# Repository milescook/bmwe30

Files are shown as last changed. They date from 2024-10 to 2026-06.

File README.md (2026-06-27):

# About

This repo is a collection of diagrams, wiring plans and 3d printable models. The objective is converting a BMW E30 to use speeduino with a digital dashboard using ts-dash. This uses the original Motronic 1.3 harness to de-risk the conversion. 

Disclaimer: Anything you follow here you do at your own risk etc.

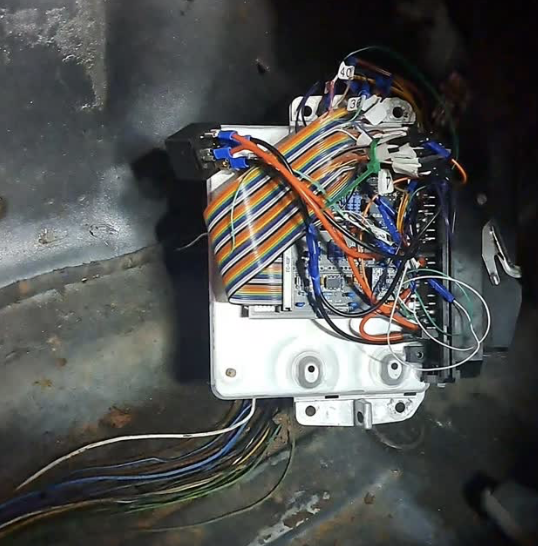
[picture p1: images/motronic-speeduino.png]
Motronic Speeduino


## Wiring
The only wiring modification needed so far, is a replacement injector sub-loom (later harnesses use a sub loom with a connector - see injector wiring for depin tool), and the TPS wires either needs an adapter or re-wire to work with an E36 variable TPS. I also converted the AFM plug to a generic connector though you could always make an adapter.

You can find a load of shorts and videos on progress here [https://www.youtube.com/cookracinguk](https://www.youtube.com/cookracinguk)

## Contents

These are the key items though take a look through the file list for bits and bobs. There's an initial stab at a custom harness for example.

- [Motronic pins to Speeduino map](docs/motronic-speeduino-map.md)
- [Cluster Conversion](docs/cluster.md)
- [Ignition module](docs/ignition.md)
- [Intake](docs/intake.md)
- [Injector wiring](docs/injector-wiring.md)
- [Main relay](docs/mainrelay.md)
- [Useful links](docs/links.md)

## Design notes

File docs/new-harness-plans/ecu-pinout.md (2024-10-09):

# ECU Pinout
* 34 pins on 4 rows, 9, 8, 9, 8. Pin number and wire colour (if present)

 [_1YE]  [_2BL]  [_3GR]  [_4WH]  [_5RD]  [_6BK]  [_7YE]  [_8BL]  [_9--]

*  [10--]  [11--]  [12BK]  [13RD]  [14--]  [15--]  [16YE]  [17BL]  
   
   [18--]  [19BL]  [20WH]  [21BL]  [22BK]  [23SG]  [24--]  [25SS]  

 [26RD] [27BK] [28--]  [29--]  [30GR]  [31RD]  [32WH]  [33GR]  [34WH]
  
## Key
* YE - Yellow
* BL - Blue
* GR - Green
* WH - White
* RD - Red
* BK - Black
* SG - Shielded ground
* SS - Shielded signal

## Pins
* 1 Injectors 1 & 6
* 2 Injectors 2 & 5
* 3 Injectors 3 & 4
* 4 Injectors 1 & 6
* 5 Injectors 2 & 5
* 6 Injectors 3 & 4
* 7 Coil packs 1 & 6
* 8 Ground (coolant, iat, lambda)
* 9 -
* 10 - 
* 11 -
* 12 - TPS Ground
* 13 - TPS Live
* 14 -
* 15 -
* 16 - Fuel pump relay
* 17 - Tacho out
* 18 -
* 19 - Coolant temp sensor
* 20 - Inlet temp sensor
* 21 - Lambda sensor
* 22 - TPS signal
* 23 - Crank position sensor ground
* 24 - CPS Shield ground
* 25 - Crank position sensor signal
* 26 - 12v Live
* 27 - 12v Ground
* 28 - 
* 29 - 
* 30 - Spare
* 31 - Oil pressure switch IN
* 32 - Oil pressure switch OUT dash
* 33 - Coil packs 3 & 4
* 34 - Coil packs 2 & 5

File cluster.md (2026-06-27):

# Overview

The objective here is a ts-dash (see http://tunerstudio.com/index.php/products/ts-dash) replacement for the instrument clocks, using the standard E30 wiring.

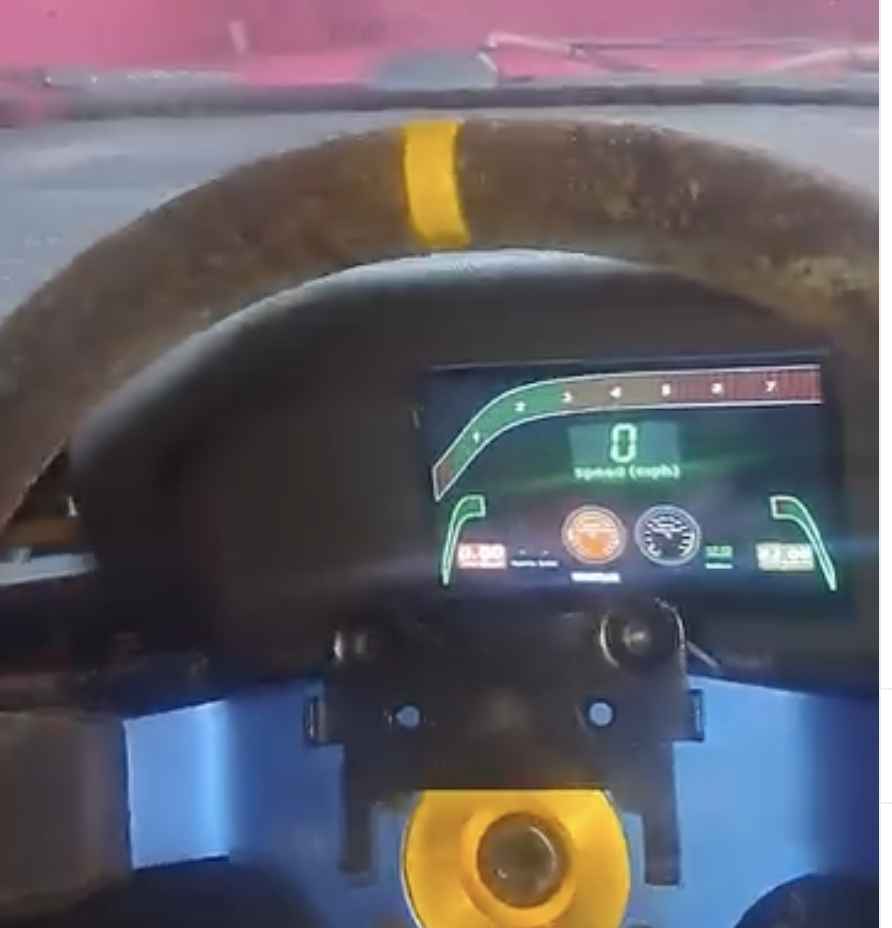
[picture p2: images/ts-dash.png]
Dash


## Pins

https://www.e30zone.net/e30wiki/images/b/b2/Instrument_Cluster.pdf

## C1 (Blue)
26 Pins

- 7 Tachometer (now Speeduino USB serial date TX from Motronic pin 6) to Pi 10 RX - Orange
- 11 Fuel flow rate (now Speeduino USB serial date RX from Motronic pin 32) to Pi 8 TX - Yellow
- 14 Alternator light +
- 16 Alternator lights -
- 18 Oil  
- 20 GND
- 23 Live 12v

# Diagrams
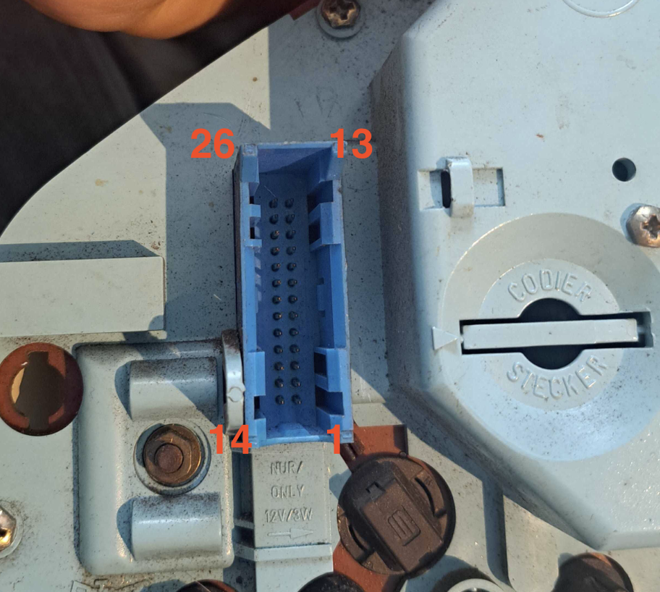
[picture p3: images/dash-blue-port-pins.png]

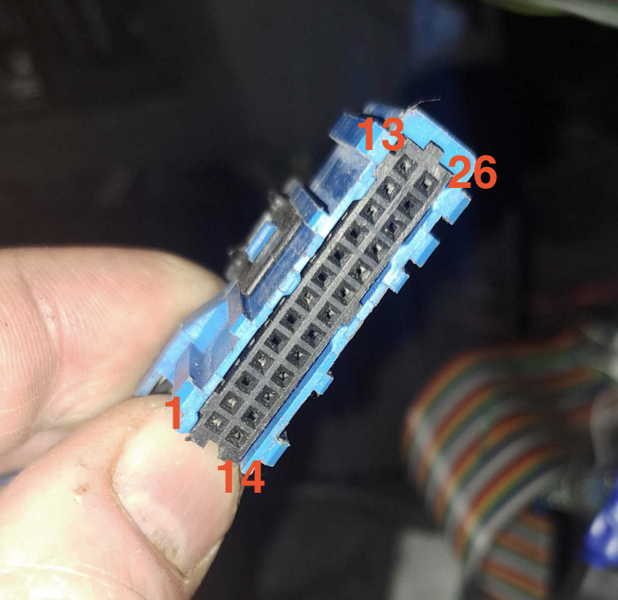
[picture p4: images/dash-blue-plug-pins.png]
Plug


## C2 (White)
26 Pins

- 4 Left fuel tank sender gnd
- 5 Fuel tank sender gnd
- 8 Speed sensor
- 13 Speed sensor

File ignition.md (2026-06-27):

# Overview

Don't make the mistake I did. Speeduino can trigger ignition either sending signal or ground - great. The E30 ignition coil is triggered by ground - fantastic. So we can use the Speeduino in ground mode, no? Erm... no. You'll find the ignition leds on speeduino just permenantly light up and you'll have no clue why...

Turns out the ignition coil is leaking live back through this (motronic 1.3 pin #1) and confuses the hell out of speeduino, so it doesn't fire. Therefore, I use a Bosch 124 ignition module.

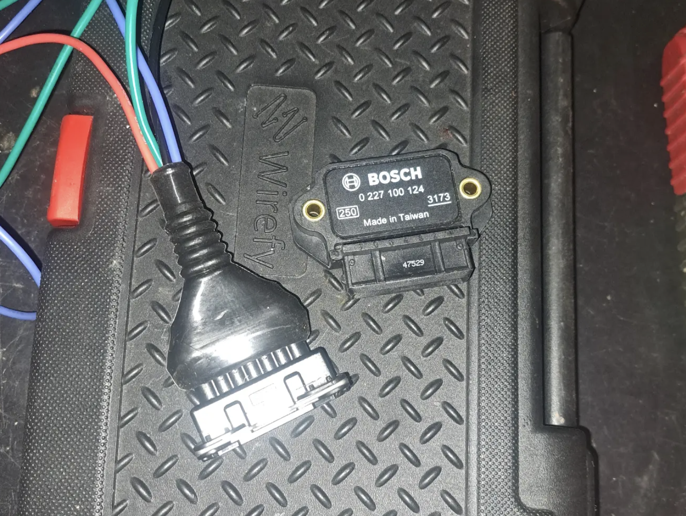
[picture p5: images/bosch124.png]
Bosch 124

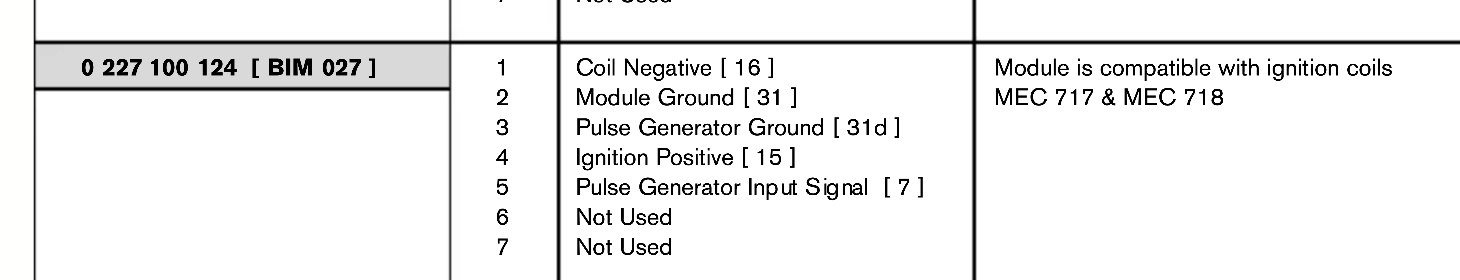
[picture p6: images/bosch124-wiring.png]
Bosch 124 wiring


**Careful!** The wiring colours in this diagram don't correspond to my own, blue and green are swapped for me.

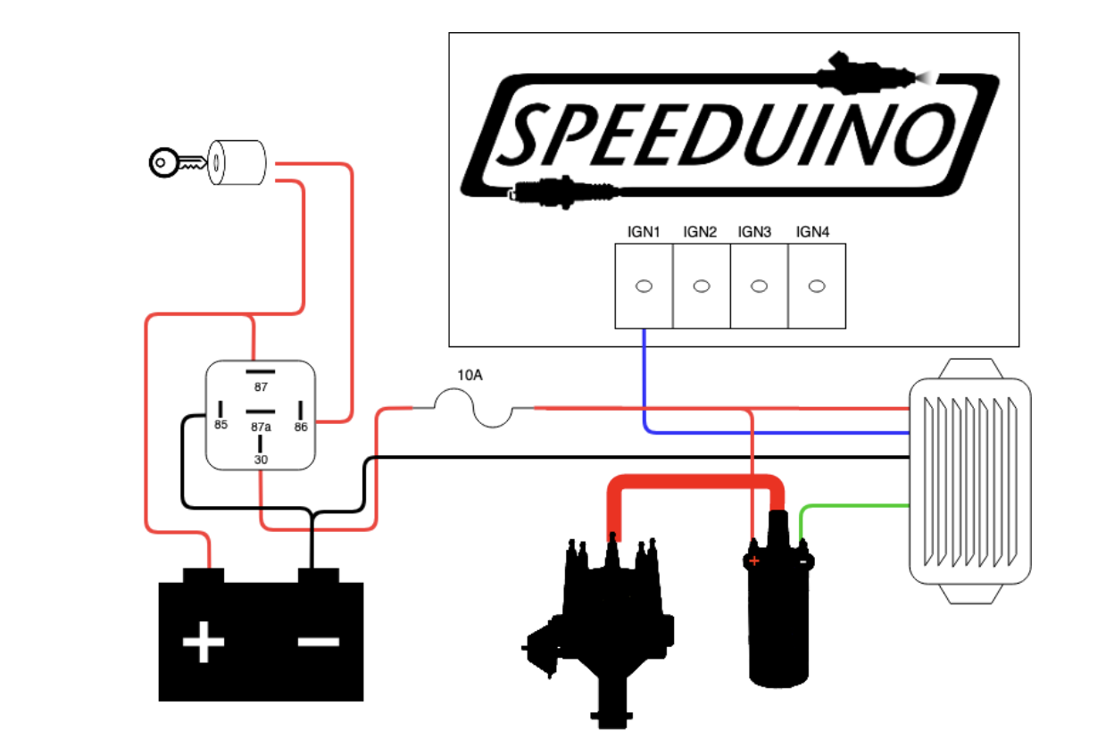
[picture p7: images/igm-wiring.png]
Ignition Module Wiring


## Ignition control module wiring
- Module pin | Purpose | Wire colour | Destination
- 1 | Coil negative | Blue | Coil black
- 2 | Module ground | Black | Chassis ground
- 4 | Ignition positive | Red | Switched live |
- 5 | Pulse generator Input Signal | Green | Ignition Coil Green wire (ground) | 

## TS Settings
Take note of these TS settings:

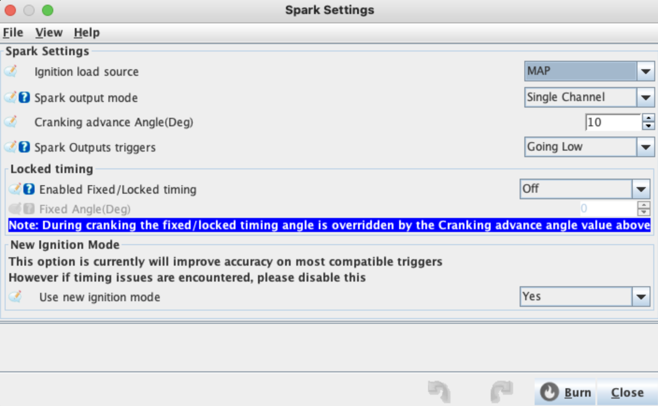
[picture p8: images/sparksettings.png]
Spark Settings


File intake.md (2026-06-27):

# Overview

The AFM is the whole reason I went down this rabbit hole in the first place... not that I needed much of an excuse. But the B25 engine didn't come with one. So erm.... new ECU with modern EFI, new cluster with wifi and live tuning, was clearly the solution :)

M20 AFM uses an outdated method of measure air intake - a physical door which measures how much air is pushing against it. So there's also a very small performance loss. Instead we ditch the AFM (it's also a couple of kg!), and use the Speeduino MAP sensor instead to measure intake air pressure. We also use an Intake Air Temp sensor to feed the Speeduino useful data.

# AFM Plug re-purpose
- Pin no - ECU Pin No - New purpose - Speeduino pin
- 1 - 44 - Inlet Air Temp (IAT) - 20
- 2 - 7 - Coolant (CLT) - 19
- 3 - 12 - Unused
- 4 - 26 - IAT / CLT Ground - 9

## M20 B20
AFM intake hose od 6.7cm

## Intake adapter

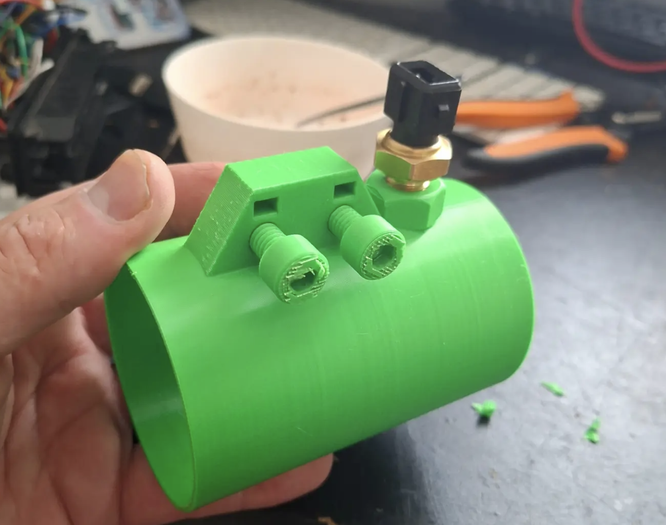
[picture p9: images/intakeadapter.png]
Intake Adapter


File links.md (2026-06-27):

# Speeduino trouble shooting

Sometimes you can't connect to speeduino, and it's required to use speedyloader to re-upload the arduino firmware. No idea why. And the Mac seems picky about what USB attachment - onloy apple will work.

# Motronic 1.3 harness <-> Speeduino pin assignment 
See [motronic-speeduino-map.md](motronic-speeduino-map.md)

# Amazing Motronic 1.3 walkthrough
https://forums.pelicanparts.com/bmw-5-series-e28-e34-e39-e60-f10-gt/534490-motronic-1-1-1-3-details.html

# Speeduino pins - ON HOLD (using a stock Motronic harness for now to reduce risk)
See [speeduino-pins.md](speeduino-pins.md)

# New ECU Loom wiring - ON HOLD (using a stock Motronic harness for now to reduce risk)
See [ecu-pinout.md](ecu-pinout.md)

# Good resource
See https://github.com/EFI-Customs/Motronic-1.3-Speeduino-Compatible-Project?tab=readme-ov-file

# Shopping list
## ECU Wiring
* 40pin connector ribbon - https://thepihut.com/products/raspberry-pi-40-pin-gpio-socket-connector-to-labelled-pins-female-150mm
* Standard ecu connectors - [https://www.ebay.co.uk/itm/334459759696](https://www.ebay.co.uk/itm/296055475113?var=594188052033)

## Sensors
See https://wiki.speeduino.com/en/wiring/system
* Wideband lambda controller and sensor - https://diy-efi.co.uk/product/14point7-spartan2-wideband
* Variable TPS from an E36 plus printed adapter plate
* IAT - https://diy-efi.co.uk/product/m12-iat-sensor
* Coolant temp sensor - will use existing blue sender
* Idle control valve -Will use existing ICV

Stuff
https://www.r3vlimited.com/board/forum/e30-technical-forums/engine-drivetrain/m42/366658-megasquirt-pinout-to-stock-ecu

# TPS Wiring

From https://www.r3vlimited.com/board/forum/e30-technical-forums/general-technical/9909959-tps-wiring

E36 TPS, pin 1 is ground, 2 is signal, and 3 is vref
E30 TPS, pin 1 is closed, 2 is ground, and 3 is open
Swap pins 1 & 2 on the E30 connector

E36 Stock wiring/TPS
1 = BRN(43) - Gnd
2 = BR/SW(12) - sig
3 = RT/GE(59) - vref

E30 Stock wiring/TPS
1 = BR/BU(52) - Closed
2 = BR(-) - Gnd
3 = BR/BK(53) - WOT

Running M5x TPS on E30 harness
1 = BR Gnd - Gnd
2 = BR/BU(52) - Sig
3 = BR/BK(53) - vRef

# Injector subloom
You can't use the existing E30 M20 injector wiring, because Motronic 1.3 firs in 2 batches of 3. Speeduino doesn't support this, and has 4 injector channels so you have to run it in paired mode, 3 pairs of 2. So instead of re-wiring the injector loom I bought this excellent depin tool (the service was fantastic) from https://falkmfg.com/products/depin-tool and made a replacement.

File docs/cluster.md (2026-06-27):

# Overview

The objective here is a ts-dash (see http://tunerstudio.com/index.php/products/ts-dash) replacement for the instrument clocks, using the standard E30 wiring.

We use a raspberry pi and lcd touch screen, and custom 3d printed dash cluster.

Dash

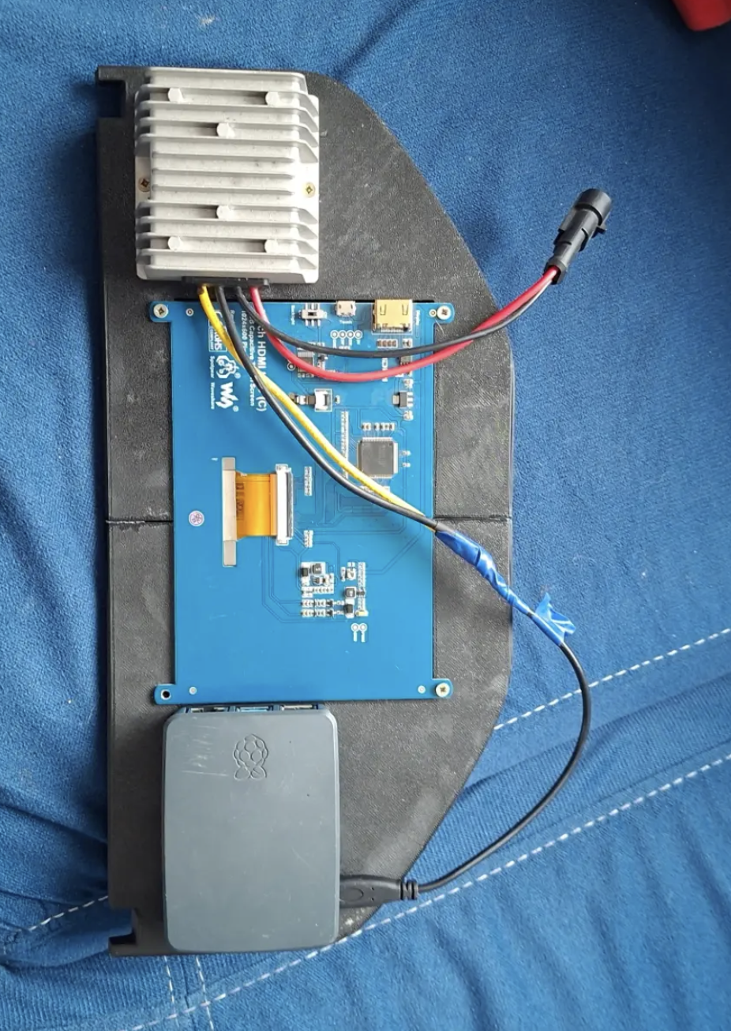
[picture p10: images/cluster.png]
Cluster

## Pins

https://www.e30zone.net/e30wiki/images/b/b2/Instrument_Cluster.pdf

## Cluster connectors

There is an stl file for the connector (tested with blue) in the stls folder. Basically it looks like below and the blue connector fits perfectly. The pins themselves are just bent dupont connectors fixed in place with a hot glue gun. Seems to work. At time of writing, more work is needed to get the locking tab to do it's job, but it certainly isn't loose.

Direct serial over the dash connectors is a non starter as pi uses 3.3v arduino uses 5v. If I can find another connection I can go via the usb plugs but can only find 3 ECU pinouts / Dash connectors

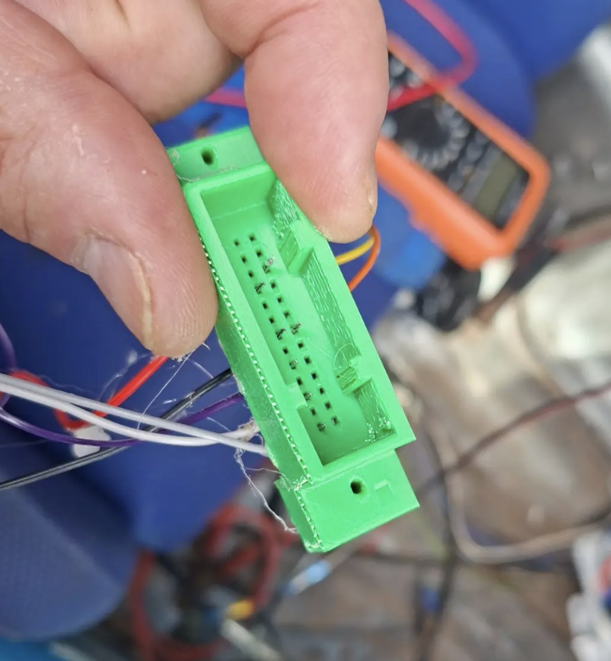
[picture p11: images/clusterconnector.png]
Cluster


## C1 (Blue)
26 Pins

- 7 Tachometer ~~(now Speeduino USB serial date TX from Motronic pin 6) to Pi 10 RX - Orange~~
- 11 Fuel flow rate ~~(now Speeduino USB serial date RX from Motronic pin 32) to Pi 8 TX - Yellow~~
- 14 Alternator light +
- 16 Alternator lights -
- 18 Oil  
- 20 GND
- 23 Live 12v

## C2 (White)
26 Pins

- 4 Left fuel tank sender gnd
- 5 Fuel tank sender gnd
- 8 Speed sensor
- 13 Speed sensor
- 22 Check Light ~~(now Speeduino USB GND from Motronic pin 16) to Pi~~

## Diagrams
Plug
Plug

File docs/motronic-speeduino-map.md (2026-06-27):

# How to map standard motronic 1.3 harness to speeduino pins (Work in progress)

WARNING: This is my wiring map, and WILL NOT work for you without harness modification. I'm re-purposing some of the ECU pins for a start, and changing the injector sub loom completely (from 2 batched to 6 individual but running as 3 pairs). I'm trying to use as much of the ECU connector as possible without changing the wiring where I can. For ignition timing I'll need a new loom anyway, as M20s used a single ignition coil and distrubtor running off the cam. I'll keep this initially for simplicity.

See https://wiki.speeduino.com/en/boards/V04 for Speeduino pins.

For the Motronic pins see  https://www.e30zone.net/e30wiki/index.php?title=ECU_Pinouts#Motronic_1.3

For comparison, see the megasquirt map here for the Megasquirt map see https://www.e30zone.net/e30wiki/index.php?title=Megasquirting_Your_M20

# Pin assignments

So you see here the map for my Motronic 1.3 harness ECU pin, to Speeduino pin, followed lastly by IDC pin. IDC is the dupont ribbon connector https://thepihut.com/products/raspberry-pi-40-pin-gpio-socket-connector-to-labelled-pins-female-150mm I have going to the Speeduino which handily labels all it's wires. Took me a while to realise that the numbers labelled have no correlation to the speeduino pins... ah well. I did make a handy map [idc-numberedpins.md](idc-numberedpins.md)

- Motronic pin  - Description - Speeduino Pin - Speeduino description - {Purpose} - IDC Pin
- 1 - Ignition Coil Output (Channel 1 - 1.1) - 7 | Ignition 1 | 28
- 2 - Ground - N/A - ECU Power relay ground, pin 30
- 3 - Fuel Pump Relay Control - 38 - Boost control (swap from 16 fuel pump as I have no ULN chip) - 35
- 4 - Idle out - 37 - PWM Idle - 33
- 5 - NA
- 6 - Tachometer output - N/A (Arduino pin 0) - ~~Speeduino USB Serial data TX (via dash plug) C1 plug pin 7 (Pi RX)~~
- 7 - AFM input pin 2 - 19 - Coolant (CLT) - 4
- 10 - Oxygen sensor (ground) - 10 - Ground - 22
- 14 - Injector gnd (???) - 12 - Ground - 18
- 16 - Injectors 1,3,5 - 2 - Injector 2 Pin 1/2 - Injector 2 - 38
- 16 - Injectors 1,3,5 - 39 - Injector 2 Pin 2/2 - Injector 5 - 37
- 17 - Injectors 2,4,6 - 3 - Injector 3 Pin 1/2 - Injector 3 - 36
- 17 - Injectors 2,4,6 - 4 - Injector 3 Pin 2/2 - Injector 4 - 34
- 19 - Main gound - ECU Power relay 85 & speeduino power -ve
- 22 - Idle out - 36 - PWM Idle 2 - 31
- 24 - Ground - 23 - Ground - 5
- 26 - AFM Common ground - 9 - Ground - IAT  / CLT Ground  - 24
- 27 - Start input- to ignition switch and coil - N/A - ECU Power relay pin 86
- 28 - O2 input - 21 - O2 Sensor - 1
- 32 - Econometer - N/A (Arduino pin 1) - ~~Speeduino USB Serial data RX (via dash plug) C1 plug pin 11 (Pi TX)~~
- 36 - Main relay output - N/A - ECU Power relay pin 87
- 37 - Switched power from main relay - NA - Speeduino power +ve in - NA
- 44 - AFM air inlet temp pin 1 - 20 - Inlet Air Temp (IAT) - 2
- 45 - Coolant Temp input - 1 - Injector 1 Pin 1/2 - Injector 1 - 40
- 45 - Coolant Temp input - 40 - Injector 1 Pin 2/2 - Injector 6 - 39
- 47 - CPS Signal - 25 - Crank Input / VR1+ - 9
- 48 - CPS gnd - 27 VR1- - 13
- 52 - Closed throttle - 22 - TPS Input - 3
- 53 - WOT Input - 13 - 5V (TPS Live) - 16

# TPS

E36 TPS Pin - E30 Pin - Purpose - Motronic pin - Speeduino Pin - IDC Pin
- 1 - 2 - GND - N/A
- 2 - 1 - Signal - 52 - 22 - 3
- 3 - 3 - Vref (5v) 53 - 13 - 16

# Other motronic pins

- 18 - Constant 12V from Battery - 12v positive (temporary power but will become unused)
- 19 - Main ground - 12v negative
- 27 - Start input - Goes to the main power relay in the new ECU case
- 36 - Main relay ground
- 37 - Speeduino power

# Lambda
- Black - Signal - ECU Loom pin 28
- White - Heater - Fuel pump live relay
- Gray - Signal Ground - ECU Loom pin 10
- Gray - Heater Ground - ECU Loom ground

# Harness side to o2 side
- Green to white
- Brown to white
- black to gray
- yellow to black

# FOR REFERENCE: Original injector subloom wiring C191 plug

- C191 plug pin no | ECU Pin | description
- 1 - 45 - Coolant Temperature Sensor
- 2 - NA - Coolant Temperature Sensor
- 3 - NA - Coolant Temperature Sensor
- 4 - NA - Coolant Temperature Sensor
- 5 - NA - DME relay (live for Fuel Injectors)
- 6 - 16 - Fuel Injectors 1, 3, 5
- 7 - 17 - Fuel Injectors 2, 4, 6

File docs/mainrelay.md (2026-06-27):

# ECU Relays

We use a relay here - nothing special just one from Halfords. The reason we do this is to work with the perfectly good E30 main relay system.

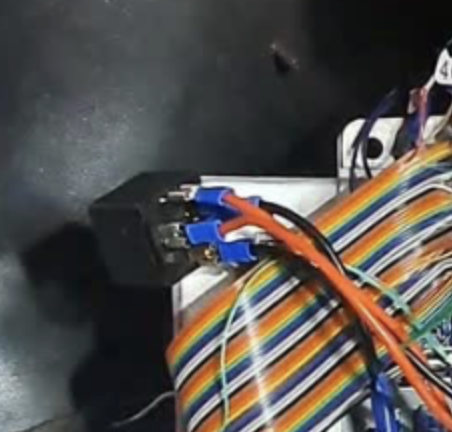
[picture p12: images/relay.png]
Main Relay


The motronic ECU when it gets power on pin 27, turns on the relay in the engine bay which in turn powers up most of the car (injectors, coil, ICV etc.). With this setup we're getting our ECU to do the same.

## How it works

When ignition is powered on (before cranking), 12v comes from pin motronic 27. This goes to pin 86 on our relay, which in turn grounds motronic pin 36, like the original ECU. This activates the main relay (in the engine bay). This in turn switches on power to motronic pin 37, which is where the speedunio live gets power from (not 27). 

It may seem a bit of a roundabout way to power the speeduino... But remember: we're powering up the car from the relay under the bonnet, and the speeduino is simply on this main circuit. It also means if your injectors and coil have no power then neither does the speeduino, so less potential troubleshooting headaches.

- ECU Pin - Relay pin - Destination / Description
- 27 - 86 - Ignition on 12v
- 19 - 85 - Motronic 19 (main gnd)
- 36 - 87
- 2 - 30 - Motronic 2 (gnd)

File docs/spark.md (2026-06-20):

From 

https://www.r3vlimited.com/board/forum/e30-technical-forums/engine-drivetrain/m20/158995-coil-ground-problem

The coil is grounded to produce a spark by the DME. Sine the ground pulses are very narrow you aren't going to get meaningful data on meter. You'd need to use an oscilloscope to look at the ground signal.

I presume that you are looking at the coil wire because the engine doesn't have spark when cranking. That being the case, run through what is below and you should be able to find the problem.

For the engine to run the following conditions must be met:

Power on DME pins:
27 Start Input
18 Un-switched Power input
37 Power Input from Main Relay

Ground on DME pins 2, 14, 19, 24

Timing data from the CPS on DME pins 47 & 48 from a rotating engine

To have spark power must be present at the coil positive and ground pulses
from the DME's pin 1 must reach the coil negative. Power to the coil is
controlled by the ignition switch via C101. When checking for spark, use the
output lead from the coil to eliminate the distributor, rotor and plug wires.

To have injector firing power must be present at each injector and ground
pulses from the DME's pin 16 (Bank1) and pin 17 (Bank2) must reach the
respective injector bank. Note that the injectors are wired as two banks of
three. With cylinder 1,3,5 being bank 1 and 2,4,6 being bank 2. Power to the
injectors is controlled by the main relay.

The fuel pump relay must have power on pin 86 (relay coil) from the main relay
output (pin 87) and power on pin 30. The DME will ground pin 85 to turn on the
relay and power the pump(s) via pin 87. Of the above, only the fuel pump power
is fused. So if the there's power at pin 87, but not at the pump, check fuse
11.

The main relay and DME pin 18 receive power from the smaller of the to wires
that connect to the battery's positive terminal. That wire incorporates an
in-line fuse. When the DME is presented with a start signal, it grounds the
main relay pin 85 and furnishes power to the fuel pump relay, injectors, and
DME.

Troubleshooting:

Disconnect the battery and the DME cable. Then:

1) Disconnect the coil negative and check continuity from that connector to
DME pin 1. Also verify that from DME pin 1 to ground is an open circuit.

2) Check the resistance across DME 47 & 48, which should be 500-560
ohms. If the CPS is dismounted, the resistance can be seen to change
from about 500 to 540-540 when a ferrous object is brought to the face of the
sensor. Neither pin should be grounded.

3) Check for continuity from DME 36 to main relay 85 and from DME 3 to fuel
pump relay 85.

Reconnect the coil, remount the CPS (air gap should be 0.040"), plug the
relays back in, reconnect the DME, and connect the battery. Then do the
following checks:

1) With the key off, verify that power is present at DME pin 18 and main relay
86 & 30.

2) With the key on, verify that power is present at DME pin 27 and pin
18. Power to pin 18 is from the main relay and there should be power to the
injectors and fuel pump relay.

3) With the key on, verify that no voltage is present at the DME grounds (2,
14, 19, 24).

4) Verify that power is present at the coil positive and at fuel pump relay
pin 30. Those get switched power from the ignition switch via C101.

The engine will start and run (if poorly) with only those connections to the
DME in place. The other signals from Cylinder ID, AFM, temp sensor, etc., are
necessary for proper operation. But they won't prevent the engine from firing.

IMPORTANT:

A power check means seeing a voltage within about a tenth of a volt of what
you measure across the batter terminals, which should be at least 12.6v on a
charged battery.

A continuity check means seeing less that 1 ohm of resistance.

An open circuit means seeing a resistance of at least 100k ohms.

A good quality auto-ranging Digital Multimeter will make these tests much
easier.

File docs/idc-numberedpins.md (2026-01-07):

## Fun fact - 40 pin IDC wire numbers don't correspond to speeduino numbers...

### IDC Ribbon number - Speeduino IDC pin number
* 40 <=> 1
* 39 <=> 40
* 38 <=> 2
* 37 <=> 39
* 36 <=> 3
* 35 <=> 38
* 34 <=> 4
* 33 <=> 37
* 32 <=> 5
* 31 <=> 36
* 30 <=> 6
* 29 <=> 35
* 28 <=> 7
* 27 <=> 34
* 26 <=> 8
* 25 <=> 33
* 24 <=> 9
* 23 <=> 32
* 22 <=> 10
* 21 <=> 31
* 20 <=> 11
* 19 <=> 30
* 18 <=> 12
* 17 <=> 29
* 16 <=> 13
* 15 <=> 28
* 14 <=> 14
* 13 <=> 27
* 12 <=> 15
* 11 <=> 26
* 10 <=> 16
* 9 <=> 25
* 8 <=> 17
* 7 <=> 24
* 6 <=> 18
* 5 <=> 23
* 4 <=> 19
* 3 <=> 22
* 2 <=> 20
* 1 <=> 21

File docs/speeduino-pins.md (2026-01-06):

    # ECU pins plug
This is a list of functions (see https://wiki.speeduino.com/en/boards/V04) and ECU connector pins - not all correspond to the Speeduino output pins

## Pin no, Function -> (IDC ribbon number) <=> harness wire # & colour
* Pin number corresponds to the speeduno IDC pin number
* IDC ribbon number is what is labelled (see table after this) as IDC numbering is different to speeduino pin numbers
* Harness wire is where it comes out of the ECU connector

* 1	Injector 1 - Pin 1/2 -> *Injector 1&6* (40) <=> 1 Yellow
* 2	Injector 2 - Pin 1/2 -> *Injector 2&5* (38) <=> 2 Blue
* 3	Injector 3 - Pin 1/2 -> *Injector 3&4* (36) <=> 3 Green
* 4	Injector 3 - Pin 2/2 -> *Injector 3&4* (34) <=> 4 White
* 5	Injector 4 - Pin 1/2 - Unused
* 6	Injector 4 - Pin 2/2 - Unused
* 7	Ignition 1 -> *Coil on plug 1 & 6* (28) <=> 7 Yellow
* 8	Ignition 4 -> *Unused*
* 9	Ground coolant, iat, lambda -> (26) <=> 8 Blue
* 10	Ground - Shield ground <=> 24 White to shield
* 11	MAP Sensor (0v-5v) *N/A - using onboard sensor*
* 12	TPS Ground 
* 13	5v power supply - TPS
* 14	Proto Area 1 (0.4.4b+ Flex Sensor)
* 15	Proto Area 2 (0.4.4b+ Fan)
* 16	Proto Area 3 (0.4.4b+ Fuel Pump) -> Fuel Pump Relay (10) <=> 16 Yellow
* 17	Proto Area 4 (0.4.4b+ Tachometer) -> AIM Dash Tacho (8) <=> 17 Blue
* 18	Proto Area 5 (0.4.4b+ Clutch)
* 19	Coolant (CLT) -> *Blue temp sender* (4) <=> 19 Green
* 20	Inlet Air Temp (IAT) -> *New IAT Sensor* (2) <=> 20 White
* 21	O2 Sensor -> *Exhaust Lambda Sensor* (1) <=> 21 Blue
* 22	TPS input -> *Variable Auto BMW TPS* (3) <=> 22 Black
* 23	Ground -> Crank ground (5) <=> 23 white shielded
* 24	Cam Input / VR2+
* 25	Crank Input / VR1+ (9) <=> 25 red shielded
* 26	VR2- (Not used for hall sensor)
* 27	VR1- (Not used for hall sensor)
* 28	5v
* 29	Idle Stepper 2B
* 30	Idle Stepper 2A
* 31	Idle Stepper 1A
* 32	Idle Stepper 1B
* 33	Ignition 3 -> *Coil on plug 3 & 4* (25) <=> 33 Green
* 34	Ignition 2 -> *Coil on plug 2 & 5* (27) <=> 34 White
* 35	Boost *N/A No snail for us, yet....*
* 36	Idle 2 (For use with 3 wire idle valves)
* 37	PWM Idle
* 38	VVT
* 39	Injector 2 - Pin 2/2 -> *Injector 2&5* (32) <=> 5 Red
* 40	Injector 1 - Pin 2/2 -> *Injector 1&6* (30) <=> 6 Black

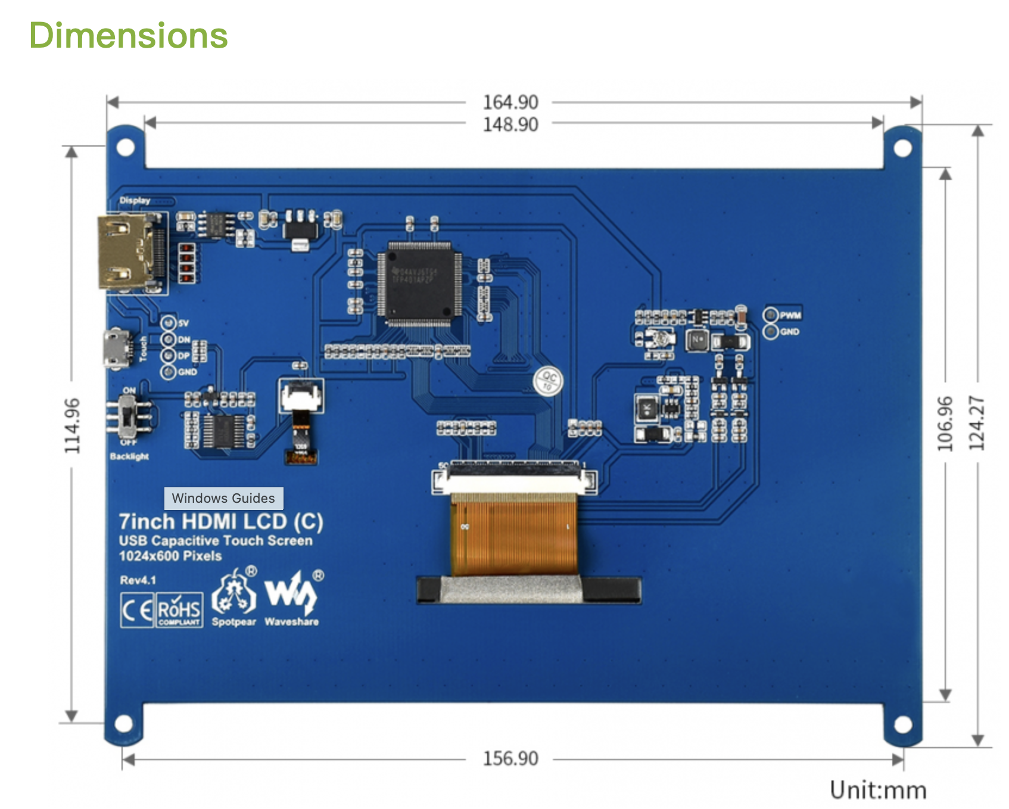
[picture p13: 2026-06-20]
images/screen dimensions.png

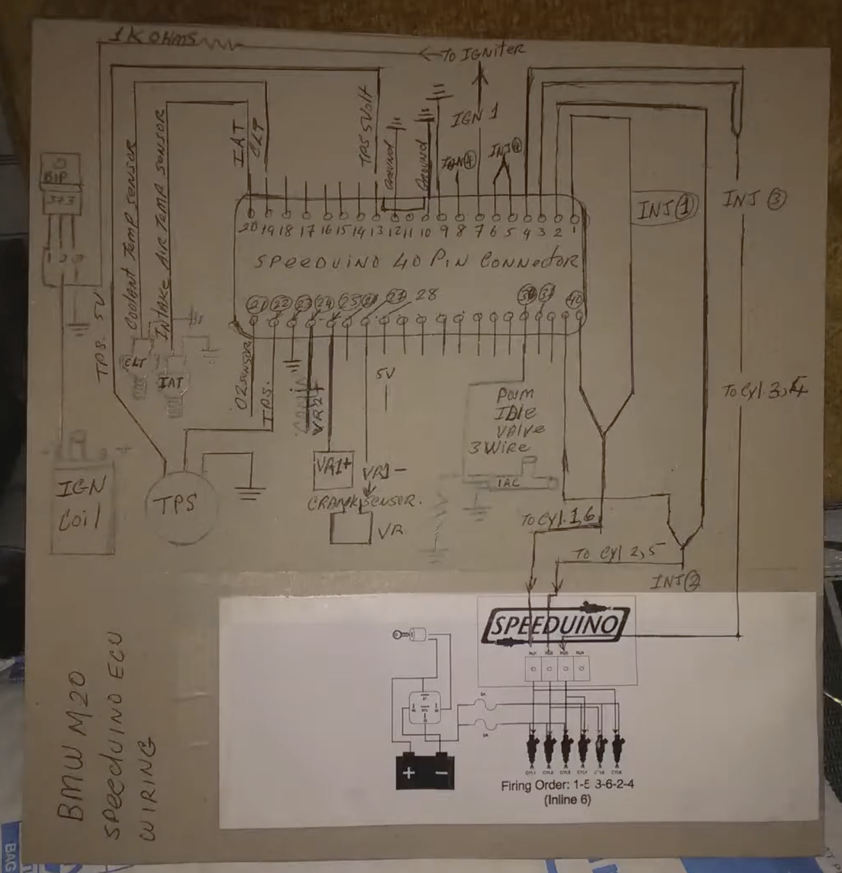
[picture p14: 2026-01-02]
images/Screenshot 2025-12-29 at 22.46.13.png

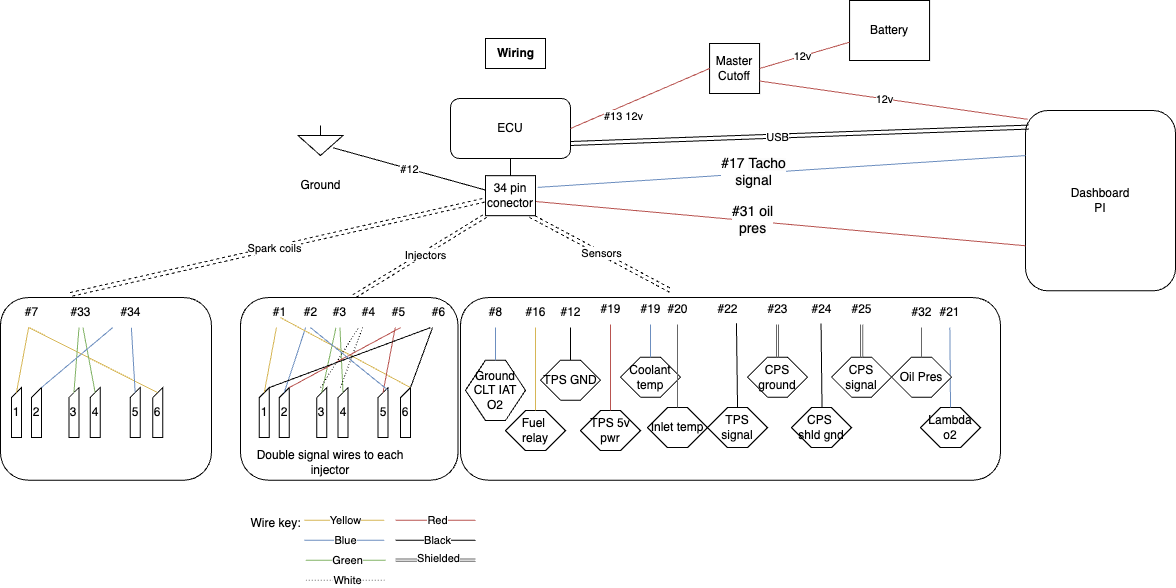
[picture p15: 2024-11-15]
images/E30 Loom.drawio.png

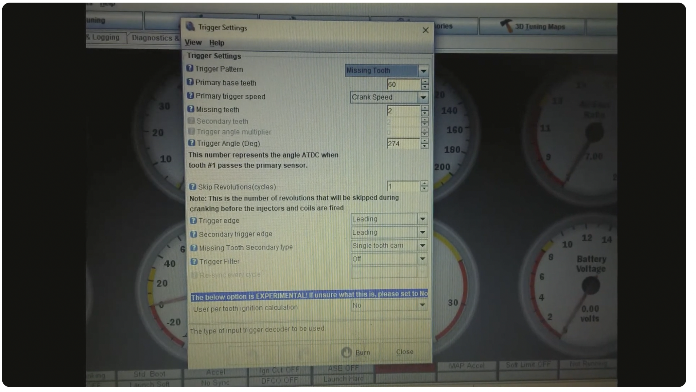
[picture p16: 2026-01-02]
images/Screenshot 2025-12-29 at 22.47.17.png

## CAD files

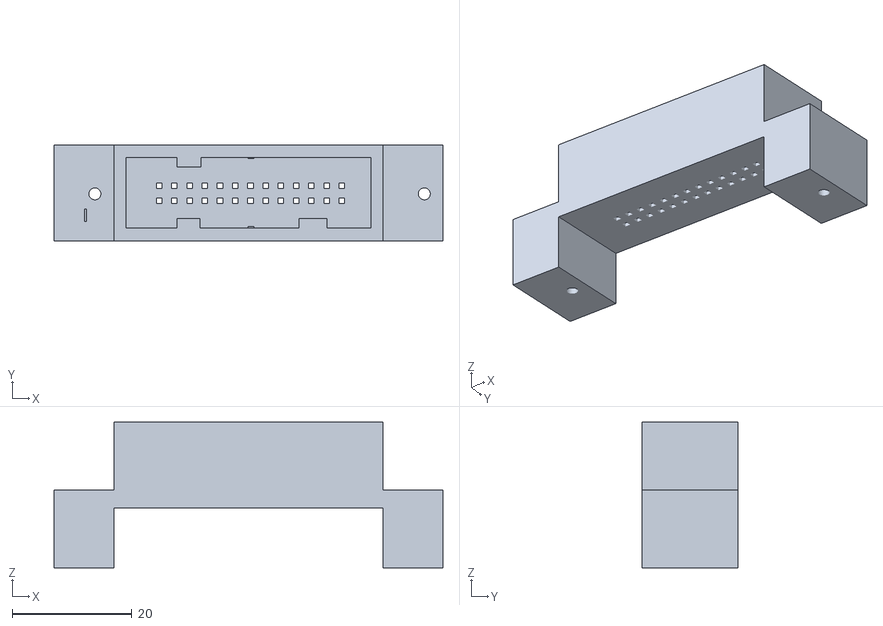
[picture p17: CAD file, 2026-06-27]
stls/dashconnector/dash-connector2.stl
64.9 x 16.0 x 24.4

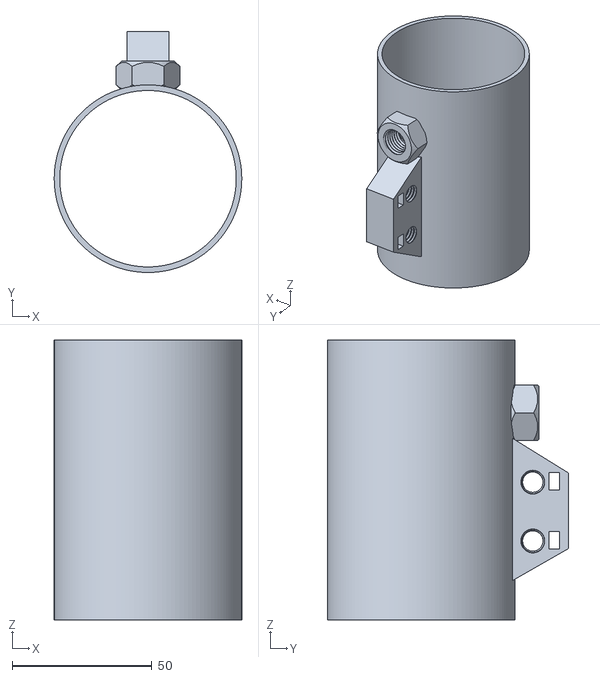
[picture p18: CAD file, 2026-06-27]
stls/intakeadapter/intake_adapter.stl
67.0 x 86.1 x 100.0

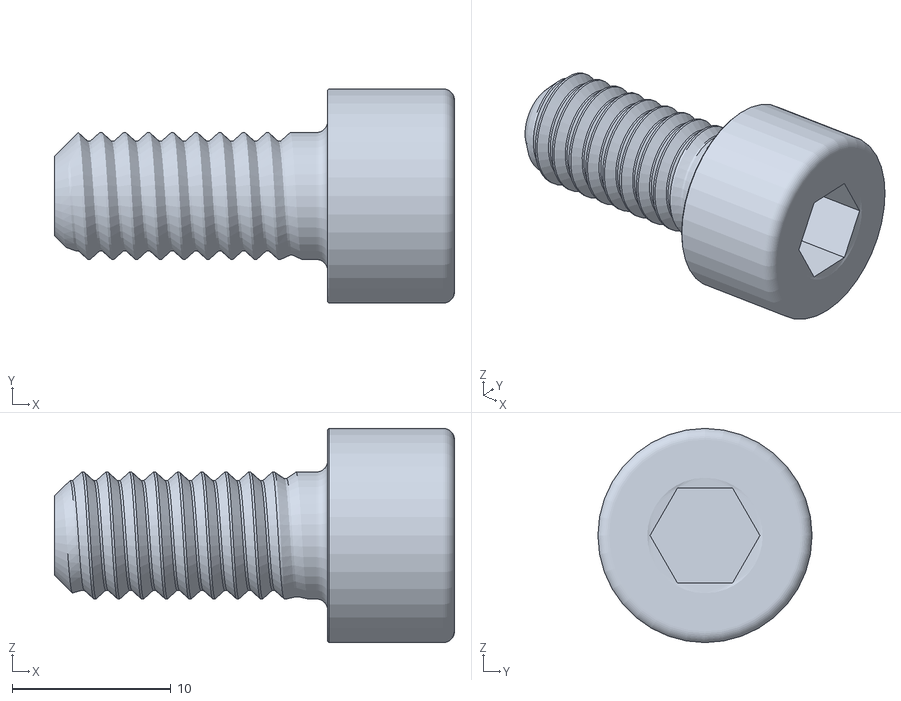
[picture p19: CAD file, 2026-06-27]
stls/intakeadapter/bolt.stl
25.2 x 13.5 x 13.5

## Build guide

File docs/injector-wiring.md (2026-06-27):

# Injectors

Basically, this wiring needs a change. You can't use the existing E30 M20 injector wiring, because Motronic 1.3 fires in 2 batches of 3. Speeduino doesn't support this, and has 4 injector channels so you have to run it in paired mode, 3 pairs of 2. 

So instead of re-wiring the injector loom, I bought this excellent depin tool (the service was fantastic) and some wiring connectors, from https://falkmfg.com/products/depin-tool so I could re-use the existing plug and make a replacement sub loom.

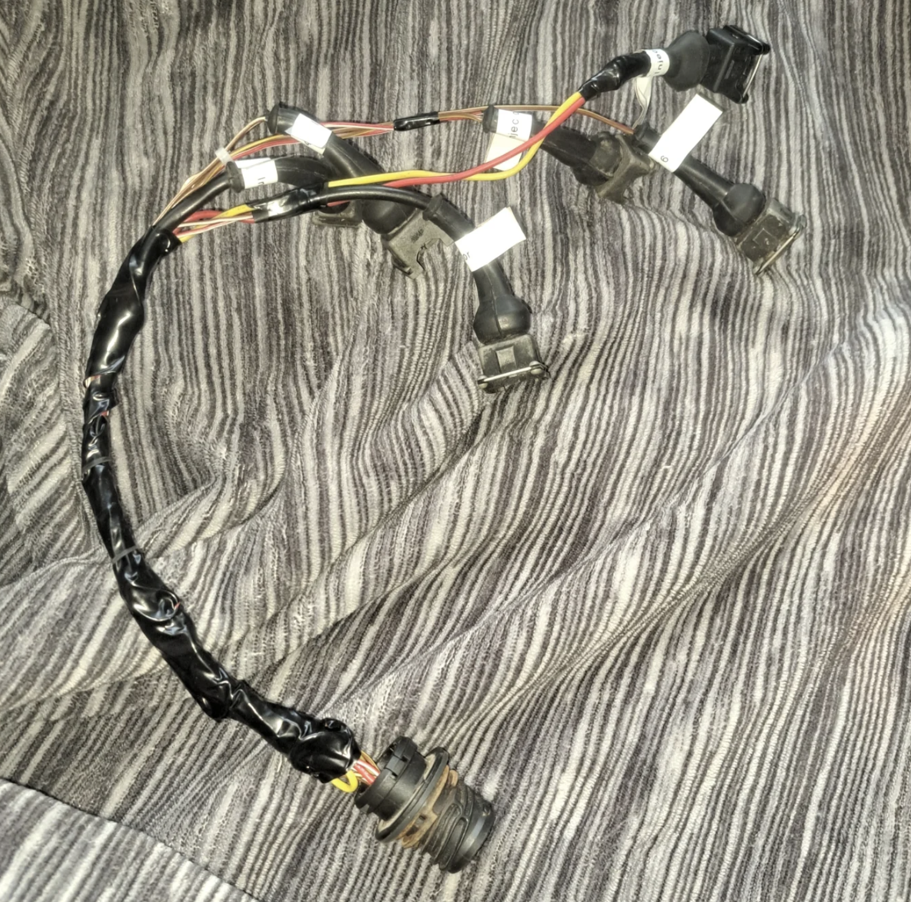
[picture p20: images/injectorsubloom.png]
Injector subloom


## Injectors connector
- Speeduino pin - Speeduino pin description - Description - ECU Pin
- 1 - Injector 1 - Pin 1/2 - Injector 1 - 45
- 2 - Injector 2 - Pin 1/2 - Injector 2 - 16
- 3 - Injector 3 - Pin 1/2 - Injector 3 - 17
- 4 - Injector 3 - Pin 2/2 - Injector 4 - 17
- 39 - Injector 2 - Pin 2/2 - Injector 5 - 16
- 40 - Injector 1 - Pin 2/2 - Injector 6 - 45

## New injector subloom C191 plug wiring

C191 Plug diagram from E30 Zone

- C191 plug pin no | ECU Pin | description
- 1 - 45 - Fuel Injectors 1 & 6
- 2 - Unused Gnd
- 3 - Unused Gnd
- 4 - Unused goes to clocks
- 5 - NA - DME relay (live for Fuel Injectors)
- 6 - 16 - Fuel Injectors 2 & 5
- 7 - 17 - Fuel Injectors 3 & 4

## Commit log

2026-01-02 Updated speeduino <-> motronic pin stuff
2026-01-07 More wiring maps inckuding AFM plug re-purpose
2026-01-20 Added more main relay info
2026-01-21 Relay pins
2026-01-21 Fuel pump relay investigation
2026-01-22 Tweaks to pins setup and added fuel new relay
2026-01-26 Rmoved fuel pump relay
2026-01-28 TPS doesn't need a clean ground, which makes things simpler
2026-02-01 Fuel pump pin switch
2026-02-04 Added cluster plug pin pictures
2026-06-20 Added thre latest tune (very baseline) and some wiring tweaks, spark updates
2026-06-27 Cluster connector tweak and STL
    [Dash Connector2.stl]
2026-06-27 Docs cleanup
    [dash-connector2.stl]
2026-06-27 power relay
2026-06-27 relay stuff
2026-06-27 relay docs
2026-06-27 relay tweaks
